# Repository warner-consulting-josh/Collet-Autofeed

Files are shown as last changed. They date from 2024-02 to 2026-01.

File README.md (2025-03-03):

# Collet-Autofeed

Automation of Collets on the Tormach Slant Pro lathe using a custom tooling block, individually addressable coolant lines controlled by an [UnexpectedMaker ProS3](https://esp32s3.com/pros3.html) and ui_hooks.py, and custom G-code for auto stock advance.

## Description

This project uses the uihooks.py [Plugin controller](http://xoomspeed.com/CNC/pathpilot/plugins/uihooks.htm) created by David Loomes at XoomSpeed, to run custom python code for interacting with a ProS3 microcontroller which in turn controls solenoids to direct the coolant stream to the currently active tool. We've also implemented custom G-code to auto advance the stock after each part with a GUI for inputting the stock length at the beginning of the run. (The stock input GUI only works on earlier versions of PathPilot, but it is not reequired for the rest of the system to function)
The hardware includes a custom tooling block, a manifold for the solenoids, a main board with the microcontroller and relays, a connector board to break out the relay lines, and enclosures for both boards.

## Getting Started

### Dependencies

* PathPilot V2
* PathPilot Plugins by [Xoomspeed](http://xoomspeed.com/CNC/pathpilot/plugins.htm)

### Installing

* Follow the instructions from [Xoomspeed](http://xoomspeed.com/CNC/pathpilot/plugins.htm) for intstalling the PathPilot Plugin framework
   * The specific plugin for running the coolant controller is [here:](https://github.com/warner-consulting-josh/Collet-Autofeed/blob/main/PathPilot%20Python/ProS3Cool_plugin.py)
* The circuitpython code that runs on the microcontroller is [here:](https://github.com/warner-consulting-josh/Collet-Autofeed/blob/main/ProS3%20CircuitPython/code.py)
   * Note that the file must be named code.py for the microcontroller using circuitpython to recognize and run it 

### Circuit Boards

* Gerber files for ordering the circuit boards are [here:](https://github.com/warner-consulting-josh/Collet-Autofeed/tree/main/KiCAD/Addressable_Coolant_Controller/gerber_to_order)
* boards were designed in KiCAD using a multi-board workflow with [KiKit](https://yaqwsx.github.io/KiKit/v1.4/multiboard/)

## Authors

Contributors names and contact info

Josh Warner  
joshua@warner-consulting.com

## Version History

* 1.0.0
    * Initial Release

## License

This project is licensed under the [GPL-3.0-only](https://opensource.org/license/gpl-3-0) License

## Acknowledgments

Inspiration, code snippets, etc.
* [XoomSpeed](http://xoomspeed.com/index.htm)
* [KiKit](https://yaqwsx.github.io/KiKit/v1.4/)
* [awesome-readme](https://github.com/matiassingers/awesome-readme)
* [PurpleBooth](https://gist.github.com/PurpleBooth/109311bb0361f32d87a2)
* [dbader](https://github.com/dbader/readme-template)
* [zenorocha](https://gist.github.com/zenorocha/4526327)
* [fvcproductions](https://gist.github.com/fvcproductions/1bfc2d4aecb01a834b46)

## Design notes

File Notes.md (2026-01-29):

# Notes

**PathPilot**

Need to find ways of ensuring that modemmanager does not kick the ProS3 into REPL
- Try this: [Addition to rules file](https://www.metrel.si/support/confluence/mpd/en/software-troubleshooting/how-to-communicate-with-instruments-under-linux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,to%20use%20specific%20USB%20device)
- and this: [rules file](https://www.downtowndougbrown.com/2016/10/fix-for-usb-serial-port-being-opened-by-modemmanager-at-startup/)
- [remove modemmanager](https://superuser.com/questions/568502/usb-device-blocked-at-startup-by-modem-manager) if the above doesn't work
- See if there is a way to ignore the commands in the circuitpython code

Need to figure out how I got custom M-codes fucntioning in the past to prompt the user for bar length and part type
- Look into remap.py and figure out what you did with it before
- Have a file named custom_m_code.py
  - Figure out how to plug this into pathpilot
  - Do I copy paste into the existing tormach remap file?
  - Do I add something to toplevel.py?
- Try following instructions [here](https://forum.linuxcnc.org/20-g-code/33642-custom-m-code-python)
- Confirmed to have working version of remapped M-codes on old pathpilot virtual machine
  - Looking into differences between two versions
  - Found some minor differences, but correcting the file in the new pathpilot did not address the issue
    - This is likely a pathpilot version difference that is causing the problem, something with Tkinter.py
  - The issue is occuring when calling M22, it seems like M20 is parsed immediately when the Gcode is loaded
    - Is my list being lost?
    - Add lots of comments/error messages to figure out where things are going wrong
- **parameter file name is missing**
  - This is caused when you comment out one of the remap definitions
  - Will cause linuxcnc to hang and become non-responsive
  - If you have anything called out as remapped in the ini file make sure it is defined in the remap.py file
- is_callable(oword.m22remap) = FALSE
  - Need to figure out how to fix this to get messages to print, probably also part of the issue in getting the dialog boxes working
  - This error is related to python files calling other python files
    - You can only go 2 layers deep before it stops functioning
    - Effecctively that means all python needs to be in remap.py because it can't call other python files properly
    - linuxcnc forum user bevins discovered this bug and it doesn't appear to have been fixed as of yet
    - likely this makes it impossible to use the custom M-code architecture for user prompting under newer versions of pathpilot
    - will check with latest release 2.10.1

**Microcontroller**
- Here's some info on the [ADC](https://docs.espressif.com/projects/esp-idf/en/v4.4/esp32s3/api-reference/peripherals/adc.html)
- Looks like the ADC is set to -11dB (full range of measurement) by [CircuitPython](https://github.com/adafruit/circuitpython/issues/8754)
  - This means that my conversion to voltage is Vin = (reading / 65535) * reference_voltage
  - Where reference_voltage is 3.3v

**Electronics**
- Relay outputs
  - Look at this [suggestion](https://electronics.stackexchange.com/questions/449872/relay-control-by-using-microcontroller) using optocouplers
    - Andrew suggested that I don't need the external BJT since the chosen optocoupler has an internal one sufficient to drive the relay directly
    - Andrew suggested to use active low signal with push pull mode if using the on board voltage regulator
      - if using a separate voltage regulator, use open drain mode with internal pull up resistor enabled
      - [here](https://docs.circuitpython.org/en/latest/shared-bindings/digitalio/index.html) is how to set the pin mode
    - added an indicator LED across the relay coil directly so that we know when the relay is supposed to be on visually
  - Relay Options:
    - [G5V-1-T90 DC24](https://www.digikey.com/en/products/detail/omron-electronics-inc-emc-div/G5V-1-T90-DC24/6650357)
  - LED:
    - [150120BS75000](https://www.digikey.com/en/products/detail/w%C3%BCrth-elektronik/150120BS75000/4489933)
  - Optocoupler:
    - [PC365NJ0000F](https://www.digikey.com/en/products/detail/sharp-socle-technology/PC365NJ0000F/720501)
- Connection to solenoids
  - VDW22JA by SMC bought [here](https://us.misumi-ec.com/vona2/detail/221006494761/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)
  - Power consumption: 3W
  - Voltage: 24 Vdc
  - Current: 125 mA
- Socket for ProS3?
  - ESP32-S3 GPIO pins each can source 40mA max, prefer to keep at 20mA (does this need power other than USB?)
- Power input
  - 3.3v or 5v for ProS3?
    - can accept both, will be getting some power from the usb (500mA?)
    - might want isolated voltage regulator for powering optcouplers? (total current draw = ?)
  - 24v for solenoids and relays

High Level Architecture
- Main board with micro controller socket, relays, LEDs, screen connection
  - Housed in waterproof enclosure with clear top, either on wall or next to operator screen
- Daughter board with relay connector sockets, big cable connector socket
  - Housed in waterproof enclosure mounted to lathe bed
  - Single cable running back to main board
- Connector board with socket for power, big cable, and USB (maybe passthrough)
  - Housed in same enclosure as Main board
  - Connects to main board with ribbon cable
  - Might instead be just snap lock connectors for power and relay control 
- Board for screen?
- Need to make diagram (draw.io?)

**KiCAD**
Need to design PCBA - Use [KiCAD](https://www.kicad.org/)
- Submodule errors:
  - If encountering this error message: `The following untracked working tree files would be overwritten by merge:`
    - Go to the offending file in the submodule directory **inside** the main project direcotry and delete it
    - **Never** add files to the submodule directory inside the main project directory, **always** add them to the submodule folder outside the project directory
    - Specifically for this project:
      - **Never** add here: `C:\Users\Josh\Dropbox\JOSHUA\Warner Consulting\Collet Autofeed\Github\Collet-Autofeed\KiCAD\Warner-Consulting-Libraries`
      - **Always** add here: `C:\Users\Josh\Dropbox\JOSHUA\Warner Consulting\Collet Autofeed\Warner-Consulting-Libraries`
    - After adding files to the correct folder, to get them to mirror to the project folder:
      - Open gitbash in the project directory
      - `git submodule update --remote --merge`
  - If encountering this error message: `This submodule has modified and untracked changes`
      - Head into the submodule's directory and make sure there isn't anything being built (an output of some kind) w/o you knowing.
      - `cd submoduledir/`
      - `git status`
  - If you see any untracked files in here, just do this to remove them:
      - `git reset --hard HEAD`
      - `git clean -fxd`
- When you need to edit a footprint, **DO NOT** use the "Edit Library Footprint..." option in the properties tab
  - Doing so will cause a conflict with the git submodule
  - Instead, open the global footprint library, make changes, then update the submodule
    - this is a bit cumbersome, but will avoid errors
    - Global and project specific libraries of the same component must have different nick-names in order to be able to edit the global library
  - If `HEAD detached` (updates in global library not reflected in project specific library)
    - `git switch main`
    - `git pull` 
- Silkscreen graphics
  - Can export .dxf from solidworks in whatver orientation I like
  - Used Photopea to create .png with stroke applied to lines and front face filled in
    - Black and white image bigger than I would like the final graphic to be on the board
  - Import .png into KiCAD image converter
    - Check the front silkscreen option and the footprint option
    - Scale to the size I want the graphic to be
    - Create new folder in the library for the new footprint and a .pretty folder inside that
    - Save the footprint in the .pretty folder
  - Push update to submodule up to github
  - Run submodule update command using gitbash
  - Add the footprint to the project specific library list
  - Add footprint onto PCB
- Multi-Board
  - not natively supported, but looks like KiKit can do it
    - install [kikit](https://yaqwsx.github.io/KiKit/v1.4/installation/intro/) using the manager inside KiCAD
    - then install [backend](https://yaqwsx.github.io/KiKit/v1.4/installation/windows/#installation-on-windows) using KiCAD Command line: `pip install kikit`
    - finally, install the [libraries](https://yaqwsx.github.io/KiKit/v1.4/installation/gui_and_libs/)
  - Set up the KiCAD project with a top-level schematic that has sub-schematics in it which each represent a board
    - The top level schematic will have the board to board connections 
  - no global labels for power or anything else, just local labels
  - [guide](https://yaqwsx.github.io/KiKit/v1.4/multiboard/#multi-board-workflow-with-kikit)
  - Board annotation for separation uses "virtual footprint"
    - kikit:board is a footprint in the library
    - Place a copy of kikit:board for each board outline
    - Rename the ref** text to the name of the board
      - **No spaces in the name** it will screw with the command for separating the boards
    - Need to make sure arrow point on kikit:board is exactly touching one of the lines in the edge cut for the board
      - use the coordinate properties from the board outline and paste them into the arrow properties
    - cd to folder containing *source_multi-PCB*.kicad_pcb
      - make sure to save board design before running command
    - run command for each board
    - `kikit separate --source "annotation; ref: *board_name*" *source_multi-PCB*.kicad_pcb *destination_single-PCB*.kicad_pcb`

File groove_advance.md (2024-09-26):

# groove_advance workflow and assumptions

**Workflow**
1. Move to starting spot (Z0)
2. Change to T81
3. Move clear in X
4. Move to end of part (Z-[#<_Groove_Start>])
5. Cut groove
6. Move to safe tool change location
7. Switch to T89 (pickle fork)
8. Move to groove and capture stock
9. Unclamp collet
10. Advance stock
11. clamp collet
12. Move clear in X
13. Move to safe tool change location
14. Change to T81
15. Cut off hat

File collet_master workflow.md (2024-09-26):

# collet_master workflow and assumptions

**Workflow**
1. Define global variables
   - #<_Length> = XX (Length of bar stock in inches)
   - #<_Remnant> = 1 (Length of remnant for collet to grip)
   - #<_Body_Length> = 1.175 (Length of Body piece)
   - #<_Nut_Length> = 0.6 (Length of Nut piece)
   - #<_Advancing_Length> = 0.283 (Length of material needed for cleanup and bar pulling)
   - #<_one_or_two> = 1 (1 = body 2 = nut)
2. User input dialog box (currently not working, need to downgrade pathpilot)
3. Part count calculation based on previously defined variables
4. Loop correct number and type of part
   - Check whether nut or body and go to corresponding subroutine
   - Run groove and advance subroutine
5. Finish program and print debug statements with number and type of parts

**Assumptions**
- Separate subroutine files for nut, body, and groove advance
- Subroutine folder path has been added to .ini file

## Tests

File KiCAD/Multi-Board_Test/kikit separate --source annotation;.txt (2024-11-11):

kikit separate --source "annotation; ref: B1" multiboard.kicad_pcb board_a.kicad_pcb

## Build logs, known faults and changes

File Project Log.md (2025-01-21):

# Project Log
Notes on what I did each day so that I can keep track of my changes and remember where/what I was working on

**01/22/2024**
- Installed Mu and plugged in TinyS3 Pro
  - Defualt code running
- Downloaded latest ui_hooks.py and installed into OLD PathPilot VM
- Commented out lines in ~/tmc/python/pathpilotmanager.py so that I don't have to pick configuration of machine every time
```
# state of the VM leftover from a previous student.
#            if os.path.exists(PATHPILOTJSON_FILE):
#                os.unlink(PATHPILOTJSON_FILE)
#                print "Removing config file to force selection of machine type in sim mode."
```
- Installed ToolPrint_plugin.py on OLD Pathpilot VM and verified it is working

**01/23/2024**
- Added "UnexpectedMaker ProS3 [0100]" to USB Device filter with USB 3.0 Controller enabled
  - CIRCUITPY drive shows up in Linux
- Added 99-ProS3.rules to /etc/udev/rules.d
```
ACTION=="add",SUBSYSTEMS=="usb",KERNEL=="ttyACM*",ATTRS{manufacturer}=="UnexpectedMaker",ATTRS{product}=="ProS3",SYMLINK+="ProS3",GROUP="dialout",MODE="0666"
```
- Modified TinyS3io.py to ProS3Cool.py and tryed to get a serial connection working
  - Plugin runs but does not successfully invoke TryToConnect()
  - Need to look into syntax and figure out why it isn't calling the function
**01/23/2024 update**
- Successfully invoked TryToConnect()
  - Previously: `self.ComPor.TryToConnect()`
  - Corrected: `self.TryToConnect()`
- Added some debug and error prevention to ProS3_plugin.py

**01/24/2024**
- Worked on getting the ProS3 to respond to data sent by the ProS3Cool plugin
- Got the microcontroller to respond to serial data sent using Mu
- Currently getting a unicode? error that causes the ProS3 to exit it's code loop and enter the REPL

**01/25/2024**
- Successfully established 2 way serial communication between the ProS3_plugin.py code and the ProS3 microcontroller
  - Needed to disable modemmanager in linux because it was causing the ProS3 to enter REPL
  - run `sudo service modemmanager stop` in the linux terminal
  - Need to investigate handling the issue in the microcontroller's code
  - Need to uninstall the modemmanager
    - `sudo apt-get purge modemmanager`

**01/26/2024**
- Worked on electronics side instead of code
  - want to get a relay output circuit put together so that I can toggle a solenoid using the code
- Got a first draft of the relay driver circuit drawn in KiCAD and approved by Andrew and Jordan
  - using optocoupler to drive a relay with an indicator LED and freewheel/flyback diode in parallel across the relay coil
  - want to use active low pins to drive the circuit according to Andrew

**01/29/2024**
- Talked with Andrew about pin modes for output
  - Want to go with push pull if using on board voltage regulator (current plan)
  - use open drain with internal pull up if using separate voltage regulator
- Verified oring sizing for manifold block using Erik online gland calculator
- Ordered oring and screws to connect top and bottom half of manifold block

**01/30/2024**
- Looked into adding a watchdog timer to reboot the ProS3 in the event of a communication failure or code error
  - Will need the watchdog timer running on the ProS3 and periodic data being sent by the plugin inside of pathpilot
  - Want to set up the pathpilot plugin to send data every ~2 seconds (pick some time interval that feels comfortable) and call feed() on the ProS3 every time data is received
- Also looked at non-blocking LED blink
  - Will want to make the responses to serial communication non blocking on the ProS3 and make the serial write commands in pathpilot nonblocking
 
**02/01/2024**
- Tried adding a watchdog timer triggered by first successful serial communication on a 2 second timer
  - 2 seconds is way too fast for development purposes, and watchdog should be triggered by a specific serial command/start phrase
  - Got stuck in a boot loop here's how to fix:
    - To get into safe mode, follow these steps:
      1. Press the [RESET] button to reset the ESP32-S3 chip
      2. After the RGB LED has gone purple and then off, press and hold the [BOOT] button for a few seconds
      Your board should now be in safe mode.

**02/05/2024**
- Adjusted watchdog timer to 45s and implemented a keyword to start watchdog ('ProS3')
  - Not sure that keyword is working as intended
  - watchdog timer stays active through resets, may need to actively disable it in code until the keyword is received
  - need to work through the logic of what should happen in the event of failure:
    - Pause the g-code running on the tormach?
    - keep the current coolant solenoid energized? or turn them all off?
    - restart g-code if connection to microcontroller reestablished?
    - wait for user input?
    - only pause if connection not reestablished with X seconds?
    - Talk with EW and make a plan
- Added `print(microcontroller.cpu.reset_reason)` to display the reason for the last time the code was stopped
  - would like to have this displayed on a screen, along with current tool, up time since last reset?

**02/07/2024**
- Removed watchdog timer and added code to toggle gpio pin based on serial input
  - Successfully implemented active low gpio triggering
- Breadboarded relay circuit but had trouble getting relay to trigger

**02/08/2024**
- Found issue with breadboard circuit
  - Flyback diode was reversed which prevented the relay from triggering
- Having some issues with the timing of the LED blink, so will need to look at difference between old and new code

**02/12/2024**
- Added KiCAD to github repository for version control and sync across computers
- Added 24v monitor circuit to circuit schematic
  - Plan to send an error/pause command up to the plugin if 24v power is lost
- Added 4 pin connector for power in of same style as ribbon cable connector that goes to the solenoid connection daughter board
  - Plan to have input daughter board with power in and USB in
- Looked at screens
  - Currently have small monochrome OLED [screen](https://www.adafruit.com/product/938)
  - Maybe want bigger [screen?](https://www.adafruit.com/product/5872)
    - Look into power requirements, and how difficult it is to drive each screen
   
**02/15/2024**
- Got KiCAD integrated fully into github using a submodule for the custom libraries
  - Created a separate repository for the [custom libraries](https://github.com/warner-consulting-josh/Warner-Consulting-Libraries.git)
  - Used git bash to add submodule to Collet-Autofeed repository which acts like a symbolic link pointing back to the libraries repository
    - `git submodule add https://github.com/warner-consulting-josh/Warner-Consulting-Libraries.git KiCAD/Warner-Consulting-Libraries`
  - Need to use `git submodule update --remote --merge` any time there are changes to the libraries repository (adding componnets, updating step files, etc.)
- Evaluated several header connectors and replaced the Wurth one with a TE AMP-Latch [connector](https://www.digikey.com/en/products/detail/te-connectivity-amp-connectors/1761685-6/2187846)

**03/01/2024**
- Successfully integrated basic display code with serial read code
  - Displayed current tool number on OLED using Mu, Pathpilot virtual machine, and actual lathe
- Need to decide what information to display
  - Current tool
  - Reason for last restart
  - Up time?
    - Will this cause issues with code blocking?
- Need to get larger screen
  - E-ink?
  - Big OLED?
  - Colored screen?

**09/03/2024**
- Powered up breadboard circuit and confirmed code works and displays current tool
  - Confirmed code working with Mu, and Pathpilot virtual machine
- Tried to get wrapper .nc program running for multiple part operation
  - Ran into issue with remapped M-Codes
  - Need to investigate further because I had this working before
  - Look into remap.py and the INI file for the lathe
  - Have python with remaps defined, need to figure out how exactly it was integrated into pathpilot

**09/05/2024**
- Worked on getting custom M-code working again
- Did not find anything terribly useful
  - Most links seem to just point back at the one post that shows how to make the M codes but doesn't have a solution to the index out error
- This was working at some point in the past
  - Maybe boot up old laptop and see if you can make it function there

**09/06/2024**
- Continued working on getting custom M-codes working
- Booted old laptop and have functioning code in onld version of pathpilot
- Same code does not work in new version of pathpilot
- Code is having trouble calling dialog = Tk()
  - When I run this on it's own in python, it works
  - It looks like pathpilot is using python 2.7, not 3.x
- Added an error message to M20 and it forced an error immediately on loading Gcode, not when I run it

**09/09/2024**
- Continued with custom M-codes
- Caused and then fixed error: parameter file name missing
  - Don't comment out any of the remaps in the remap file
- Currently dealing with is_calable(oword.m22remap) = FALSE
- Stripped the remapped M-code functions down to only displaying messages that they were called, but no message shows up, likely due to the above
- Probably also part of why the dialog boxes are not functioning
- Further research on the linuxcnc forum required

**09/10/2024**
- Figured out how to snapshot virtualbox
- Updated pathpilot inside virtualbox to latest version 2.10.1
- This erased my changes in the .ini and custom M-code stuff, so I will need to re-introduce them to test if this still has the issue with nested python calls

**09/24/2024**
- As far as I can tell, I will not be able to get user prompting running under later versions of PathPilot
  - Will need to revert machine to v2.2.4 (figure out latest version that will work)
- Got subroutine code working
  - Needed endif statement for every if statement (elseif does not function as endif)
  - Needed endsub for one of the routines
- Got external named subroutine working
  - Needed to add subroutine path to .ini file
  - Need to make sure subroutine file is executable
  - o<filename> sub/endsub/call (where filename is the name of the subroutine file without the .nc extension)
- Moved groove and advance code into external subroutine
- Need to move body and nut code into external subroutines
- Need to add grooving stock requirement to part per bar calculations
- Need to add part number override for running n parts explicitly until we get user prompting working

**09/30/2024**
- Got the code transfered over to the lathe and have collets running multiples at a time
  - Need to copy the working code from the lathe into the github so that it is accurately represented
- Looked at the state of electronics
  - Enclosure and connectors that I had previously ordered
  - Drew a crude architecture diagram, need to transfer that into a more refined format draw.io?
  - Plan to have small enclosure on lathe bed with connections to relays on a board that connects to a larger (10 pin) cable
  - 10 pin cable connects to main board in housing that is stationary
    - Either mounted on wall or on operator console
  - Main board enclosure has screeen, relays, microcontroller, power connection, relay control connection, USB connection
    - USB will be pass through (have gland pieces)
    - Power and relay control will be snap lock type connectors
    - No ribbon cable, no daughterboard in this enclosure
    - Will need to mount screen in here somehow
      - Don't want to block relay LEDs
      - Can use little connector cable directly from micro, or could use pins and headers
     
**10/03/2024**
- Drew a basic architecture diagram in draw.io
- Started designing relay connector board and enclosure
  - Will use 10 pin connector and snap lock to connect to PCB with 8x 2 pin connectors
  - Plan to machine enclosure from solid piece of delrin and use O-ring to seal lid
    - 3D print before machining to ensure everything fits
   
**10/08/2024**
- Finished design of relay connector board enclosure
- Need to double check O-ring gland design
- Will be machined from large block of delrin with clear acrylic lid
- Need to adjust mounting board to fit new design
- Need to work on PCB layout for connector board
- Need to work on design of enclosure for main board with screen

**10/11/2024**
- Tried using big screen, looked like more effort than I was up for this morning
- Do we actually need big screen?
  - Screen is more of a diagnostic tool/passive information display
  - Focus should be on getting system functional and then adding features later if we want them
  - Design enclosure for small screen and deal with big screen later
- System is fucntioning, so we should get some PCBs and enclosure
- Need to machine solenoid manifold
- Need to machine connector board enclosure

**10/14/2024**
- Added `ignore = dirty` to gitmodule file to deal with untracked changes issue in github
- Started placing components into mcmaster washdown enclosure, but had to deal with github issues for most of the morning

**10/15/2024**
- Replaced ribbon cable connector with 10-pin molex connector on main board schematic
- Started placing connectors and board supports in mcmaster enclosure model
- Fixed issues with libraries and added library for molex connector
- Need to double check that libraries are properly syncing because one of my footprints was missing
- Need to add board clearance to board support piece

**10/17/2024**
- Actually fixed issue with submodule
  - Had created file inside mirrored folder instead of in base repository folder, see notes for details
- Added 2 pin power connector to schematic
- Updated board outline to new size and started positioning components

**10/22/2024**
- Placed components on PCB and completed initial routing
- Still need to add power and ground planes
- Need to figure out why labels are not showing on silk screen
- Need to add silk screen demarkations for solenoid to LED correlations
- Probably should add a logo and some other identifying information to the silk screen as well

**10/23/2024**
- Replaced PC365NJ0000F surface mount opto-isolator with PC12311NSZ1B through hole
- Added power and ground fills on top and bottom layers respectively
- Need to figure out why changes to 10-pin and 2-pin connectors didn't save/propagate to other computer
- Need to figure out silkscreen labels not showing for components

**10/24/2024**
- Added rectangle representing screen into the silkscreen layer
- Sketched screen board outline in solidworks in the part file of the box
- Need to figure out screw size and standoffs
- Need to add screw holes into main board
  - Consider 3d printed screen support as alternative
  - Might be somewhat spidery, but maybe it would work with standoffs
 
**10/25/2024**
- Fixed silkscreen labels for components
  - Had to mess with library footprints and update the footprints on the pcb
- Replaced remaining surface mount opto-isolator with through hole
- Adjusted screen mount to used OTS standoffs

**10/28?2024**
- Figured out how to add custom silkscreen graphics
- Added logo to silkscreen
- Fixed issue with step file of LEDs disappearing

**10/29/2024**
- Added zones and zone labels to silkscreen
- Added "Addressable Coolant Controller v1.0.0" to silkscreen
- Added company name, my name and date to silkscreen
- Need to make connector board and model screen into assembly
- Need to review finalized board before sending for manufacturing

**10/30/2024**
- Changed name of KiCAD project to Addressable Coolant Controller
- Moved KiCAD files into subdirectory named per previous
- Looked into multi-board project workflow in KiCAD
  - is not natively supported, but the plugin KiKit can do it
  - installed KiKit and will try doing a multiboard project
  - want to have main board and connector board with shared pinout for connector between them
 
**10/31/2024**
- Created Multi-Board Test project to figure out the multiple board in one project workflow
- Made top level schematic with inter-board connector and heirarchical labels to pass pins down into each board sheet
- Made one PCBnew file with both boards in it
- Need to figure out annotation for board separation
  - Something about "virtual footprints"

**11/04/2024**
- Got multi-board workflow functioning on a test project
- Added instructions to notes.md on how to implement this workflow
- Dad asked to add pressure sensor to system to detect coolant flow

**11/05/2024**
- Ordered pressure sensor from amazon
  - 0.5v-4.5v output, 5v input, 100psi max
  - 3 wires: VCC, GND, Output
  - will need a voltage divider to step down to 3.3v for ProS3
  - will need to implemnet code to read signal input
 
**11/07/2024**
- designed voltage divider low pass filter circuit
  - chose 10Hz as cutoff freq
  - resistor and capacitor values in Parsify file
- looked at 12 pin connectors for accomodating the pressure sensor on the connector board
  - omron internal connectors come in 12 pin variant -> easy change
  - found 12 pin circular connector from Amphenol
    - need to evaluate the size impact on connector board enlcosure
    - components to make a cable are ~$175
    - premade cables are out of stock but only ~$30 -> 4 week lead time from mouser

**11/08/2024**
- found 4 pin connector for pressure sensor
  - same family as 2 pin connectors for solenoid connections
- added 9th hole in connector enclosure for pressure sensor connector
- added 12 pin connector to connector board assembly
  - need to adjust sketch to match dimensions of new connector
- added 12 pin board connector and adjusted sketch to match
  - needed to modify 10 pin connector because SnapEDA kept downloading the wrong one for the 12 pin
  - will need to add to the library repo
  - will need to double check footprint
- ordered 12 pin connector, 12 pin board connector, 12 pin board connector mate, short 12 pin cable, 4 pin connector, 4 pin cable
- ordered long 12 pin cable from mouser on backorder, 4 week lead time
- main lathe assemlby is broken and will not open on my computer, will need to remake
- discussed overall assembly of tooling block, solenoid block, and connector board assembly on big plate
  - want to be a complete unit
  - need to make it easier to put on and off the lathe
  - want to reduce swarf build up in lower corner

**11/13/2024**
- got footprint and symbol customization workflow ironed out
  - have global libraries of symbol and footprint
    - tied directly to the Warner-Consulting-Libraries repo
    - changes here update the repository
  - after updating the repository files, update the submodule and the changes will be reflected
- put 12 pin connector into top level schematic
- added voltage divider circuit into sub sheet and add heirachical label sheet pins to pass the nets in and out
- assigned IO13 to reading the output from the pressure sensor off the voltage divider
- fed 5v out from the MCU to power the pressure sensor
  - pressure sensor is stated to draw ≤3mA, should be safe to power from MCU
- will need to double check component values for voltage divider and order them
- will need to export board outline from solidworks with placements for the connectors
  - will need to figure out how to line up connector footprints with specified locations on board outline

**11/14/2024**
- measured pressure response of 100psi pressure sensor
  - very linear, made an excel sheet to visualize data
  - output is ratiometric to input voltage
    - this means I can use 3.3v to power it and won't need a voltage divider for the GPIO
- want to use a 30psi sensor instead
  - ordered one on amazon in same form factor
- fixed the broken netclasses in the schematic
- removed the voltage divider circuit and heirarchical sheet
- added some info to the title block of the sheet
  - need a version of the logo with no color in the background
  - could also make it a blue logo

**11/15/2024**
- ordered solder cup version of 12 pin connector
- fixed 12 pin connector sketches in connector board skeleton
- sized oring gland in connector board skeleton
  - make sure that the connector board with all components is able to slide in from the top
  - make sure oring gland is sized for off the shelf oring
- need to make keying feature on 12 pin connector cutout

**11/18/2024**
- made subassembly for entire tooling plate with block, solenoid manifold, and connector board
- adjusted 12 pin connector cutout to have proper shape for keying
- sized o-ring gland for both solenoid manifold and connector board housing
- made simplified slant pro assembly
  - need to adjust range of motion in assembly and finish making the moveable comonents

**11/22/2024**
- added connector board outline and circular connector locations to the pcb file
- updated schematic with circular connectors and added the propper netclasses
- added libraries for the circular connectors
- updated pcb with changes from schematic and now I need to fix the routing and placement of components
  - component designators got moved around and now components are all scrambled on the board

**11/25/2024**
- updated all component designators and locations on board
- fixed netclass issues and rerouted all ratsnest items
- routed connector board
  - need to add copper fills for ground plane
- need to fix missing 3d models on some LEDs
  - probably need to update the LED footprints at the library level (global library tied to the repository)

**11/26/2024**
- added LEDs to connector board
- moved LEDs and accompanying resistor and connector into heirarchical sheet for easy circuit and layout duplication
- fixed LED footprints and missing models
- added board outline annotations for splitting using kikit
- exported step file and added to solidworks subassemblies
- need to get a top level assembly functioning
- need to redo pressure characterization with 30psi sensor
- need to start coding the pressure sensor into the microcontroller
- finalized board designs and sent to JLCPCB for manufacture
  - shopped around and they were by far cheapest
- made Warner Consulting logo a soldermask/copper logo and use ENIG for gold apperance on final board
  - [copper graphic element](https://forum.kicad.info/t/shouldnt-copper-only-symbol-footprints-have-have-solder-mask-removed/45087/2)
- added "Designed in KiCAD" logo as a copper element for subtle effect
- do we want to make this design open source?

**12/02/2024**
- Created interactive HTML BOM using KiCAD external plugin
- ordered remainder of board components
- want to 3D print connector board enclosure and assemble with fasteners and oring
- want to 3D print main board mount and screen mount
  - need to order fasteners, standoffs, and enclosure from McMaster

**12/11/2024**
- Over the last few work days I have populated 1 each of the main board and connector board
- Fit checked the connector board in a 3D printed enclosure with laser cut lid
  - laser cutter needs some sort of calibration/maintainence, it was cutting oversized and out of square
- ordered wires and ferrules to make wiring harness for connector board and main board
- ordered slightly-nicer-than-amazon-quality ferrule crimpers from Ferrules Direct
- started 3D print of manifold block to fit check
- fit checked manifold block with all solenoids and pressure sensor
  - still need to get input fitting and o-ring
  - still need to check the press-in push-to-connect fittings, but the print geometry was not good in that area
  - reprint a single widget with those holes facing upwards

**12/13/2024**
- Adjusted design of screen mount and printed so that screen avoids gate in clear enclosure lid and also logo
- made wiring harness for 24v from bench power supply for testing code changes without being hooked up to lathe
  - crimp on bootlace ferrules work beautifully in omron connector, insulation is perfectly sized
- started widget print for fit checking the press-in push-to-connect fittings

**12/16/2024**
- Mapped pins in code to board pins and tested function with main board
- Added power monotor code
  - will need to figure out how to pass this info back to linuxcnc
  - will need to figure out how to pass current tool info back to linuxcnc (heartbeat? watchdog? look more deeply into this)
- need to figure out how to map tool numbers to solenoid numbers (dynamically?)
  - look at having a preamble in the gcode or something in the python plugin code to communicate this info to the microcontroller
- Added first step towards having pressure sensor

**12/17/2024**
- Received wires from wire barn
- Started organizing all hardware into Sortimo project box
  - Using label maker for each bin with description, PN, applicable tool, material, QR code link, etc.

**01/01/2055-01/06/2025**
- Wired pressure sensor up to the 4 pin connector and added code to microcontroller to read ADC input
  - Need to convert raw ADC value to PSI value
  - Need to measure ADC value with known pressure to create calibration curve
- Organized electrical components into Sortimo box with labels
- Need to make cutouts in enclosure for connectors
- Need to machine Connector Board enclosure
- Need to machine solenoid manifold block

**01/09/2025**
- Used ChatGPT to transition existing PathPilot plugin code into a state machine format
- Created stat transition diagram and used Draw.io to digitize it
- Will need to test the code to prove functionality
- Need to transition microcontroller code to state machine and define what messages to send back to the PathPilot plugin

**01/10/2025**
- Got the state machine architecture working on for the PathPilot plugin
- Used ChatGPT to transition the microcontroller code into a state machine format
  - Will need to creat state transition diagram for microcontroller code
- Having some issues with funky messages received by the PathPilot plugin
  - need to figure out exactly what the microcontroller is sending and clean that up
- Want to have tool number verification
  - want the PathPilot plugin to get confirmation that the microcontroller has the correct tool

**01/20/2025**
- Got the microcontroller sending it's tool number, power status, and pressure data periodically out over serial
- Plugin code now listens to that data and has some error responses
  - If program is running and power has been off for X seconds, stop the program
  - If program is running and tool number received does not match that in the spindle (after X second delay), stop the program
- Need to convert pressure integer data into PSI
  - Then need to do something with that
    - Check if coolant is supposed to be on, then check if pressure has been trending down/goes below a threshhold, then stop the program
- Need to look at disconnection failures and attempting to reconnect

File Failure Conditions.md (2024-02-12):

# Failure Conditions and Response Strategies
**Failure Modes**
1. Power loss to microcontroller
2. Power loss to solenoids
3. Code crash
4. Serial communication lost

**General Thoughts**
- Not haveing coolant isn't like not having air, more like not having water
  - Need to fix the problem, but don't need to stop instantaneously
  - Have ~30-60s to respond?
- Want to check status of microcontroller after each operation?
  - Don't like that this needs to be added to the G-code
    - might be able to detect an operation change similar to how a tool change is detected
    - don't like the variability in length of time of the operations (time without coolant could be as long as longest operation)
  - Would prefer to have the status check built into the plugin
- Want to check the status of microcontroller every X seconds?
  - "Hearbeat" sent from microcontroller and listened to by plugin
  - Watchdog timer on microcontroller to reset in case of code failure
- How many times/how long should plugin try to reconnect before issuing a pause command?
  - use "TryToConnect" function for X seconds or X times
- Should we have a fallback coolant nozzle that is fixed to the headstock?
  - turns on if there are issues with the plugin/microcontroller
  - allows finishing current part?
- Want to display message about why the microcontroller failed/reset/restarted
  - send message to plugin
  - also display on small screen directly on microcontroller
  - have a running timer showing how long the microcontroller has been functioning since last reset

**Response Strategies**
1. Power loss to microcontroller
   - leads to serial communication lost
   - try to reestablish communication within acceptable time frame using plugin code
   - else, pause program 
3. Power loss to solenoids
   - leads to no coolant flowing from nozzles
   - could have fallback nozzle that is "fail safe" ie. is the default path that is diverted away from when a solenoid is powered
   - want to feed info about solenoid power back into microcontroller
   - if power not restored to solenoids within X seconds, send pause message to plugin
5. Code crash
   - leads to serial communication lost
   - use watchdog timer to reset microcontroller
   - try to reestablish communication within acceptable time frame using plugin code
   - else, pause program 
7. Serial communication lost
   - try to reestablish communication within acceptable time frame using plugin code
   - else, pause program

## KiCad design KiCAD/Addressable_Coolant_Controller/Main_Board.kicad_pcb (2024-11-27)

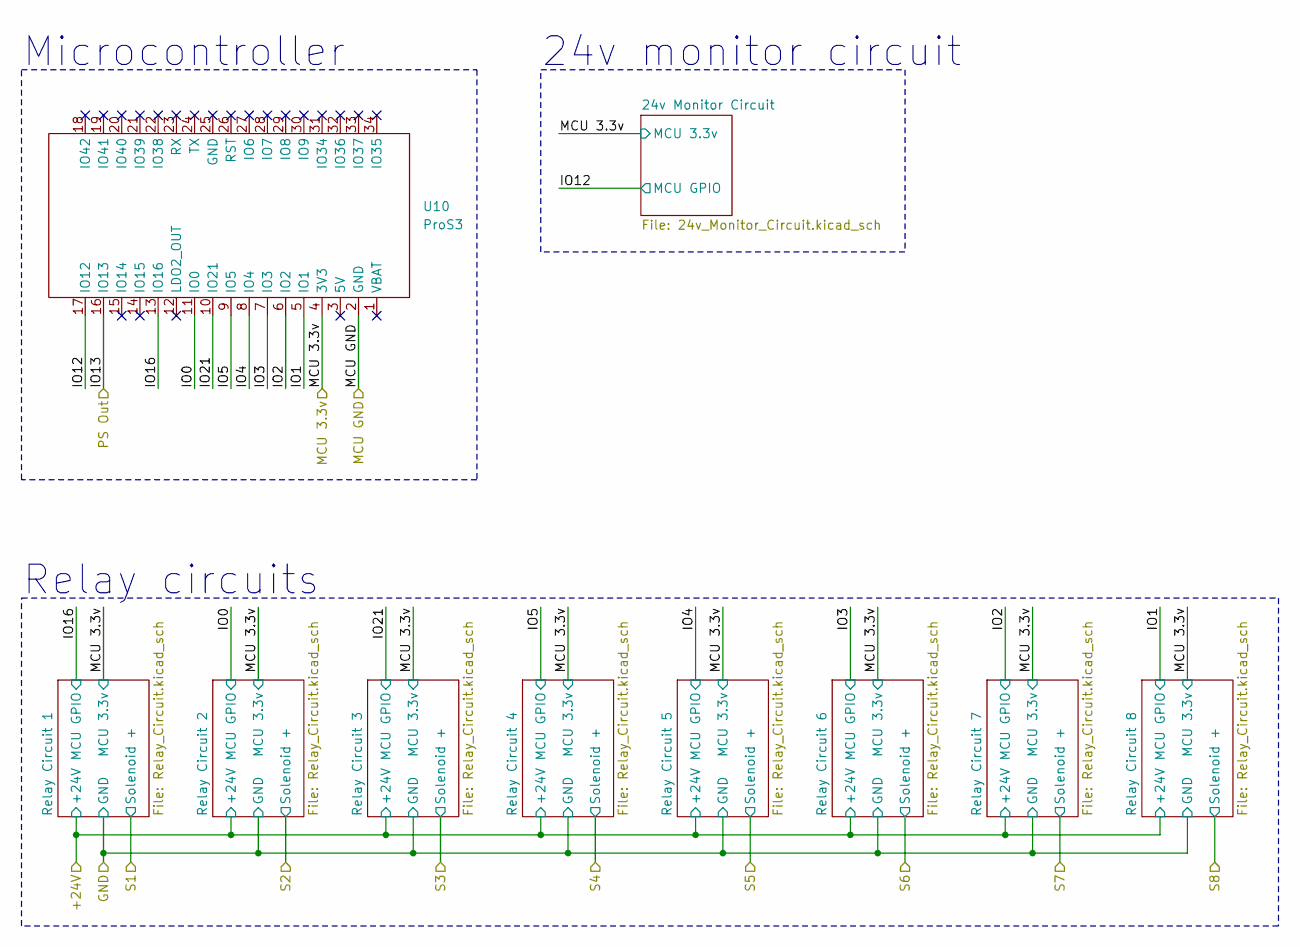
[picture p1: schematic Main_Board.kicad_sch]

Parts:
U10: ProS3; ProS3_TH

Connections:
/Main_Board/IO0: U10.11 (IO0); also elsewhere on the board
/Main_Board/IO1: U10.5 (IO1); also elsewhere on the board
/Main_Board/IO2: U10.6 (IO2); also elsewhere on the board
/Main_Board/IO3: U10.7 (IO3); also elsewhere on the board
/Main_Board/IO4: U10.8 (IO4); also elsewhere on the board
/Main_Board/IO5: U10.9 (IO5); also elsewhere on the board
/Main_Board/IO12: U10.17 (IO12); also elsewhere on the board
/Main_Board/IO13: U10.16 (IO13); also elsewhere on the board
/Main_Board/IO16: U10.13 (IO16); also elsewhere on the board
/Main_Board/IO21: U10.10 (IO21); also elsewhere on the board
/Main_Board/MCU 3.3v: U10.4 (3V3); also elsewhere on the board
/Main_Board/MCU GND: U10.2 (GND); also elsewhere on the board

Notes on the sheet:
Microcontroller
24v monitor circuit
Relay circuits

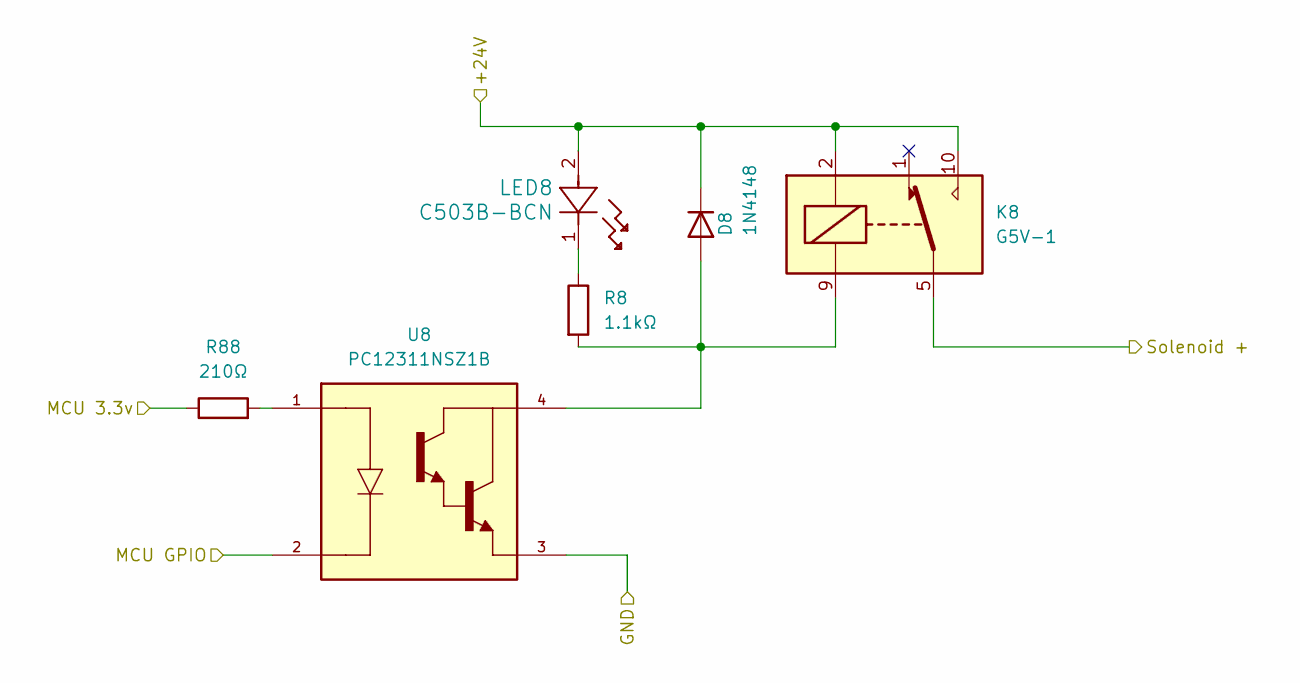
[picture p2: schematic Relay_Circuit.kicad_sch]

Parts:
D8: 1N4148; D_DO-35_SOD27_P7.62mm_Horizontal-JW
K8: G5V-1; Relay_SPDT_Omron_G5V-1
LED8: C503B-BCN; C503B_BCN_CV0Z0461
R8: 1.1kΩ; R_Axial_DIN0204_L3.6mm_D1.6mm_P5.08mm_Horizontal-JW
R88: 210Ω; R_Axial_DIN0204_L3.6mm_D1.6mm_P5.08mm_Horizontal-JW
U8: PC12311NSZ1B; Mouser Part Number 852-PC12311NSZ1B

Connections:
+24V: D8.1 (K), K8.2, K8.10, LED8.2; also elsewhere on the board
/Main_Board/IO1: U8.2; also elsewhere on the board
/Main_Board/MCU 3.3v: R88.1; also elsewhere on the board
/Main_Board/S8: K8.5, K8.6; also elsewhere on the board
GND: U8.3; also elsewhere on the board
unnamed: D8.2 (A), K8.9, R8.2, U8.4
unnamed: LED8.1, R8.1
unnamed: R88.2, U8.1

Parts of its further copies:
D1, D2, D3, D4, D5, D6, D7: 1N4148; D_DO-35_SOD27_P7.62mm_Horizontal-JW
K1, K2, K3, K4, K5, K6, K7: G5V-1; Relay_SPDT_Omron_G5V-1
LED1, LED2, LED3, LED4, LED5, LED6, LED7: C503B-BCN; C503B_BCN_CV0Z0461
R1, R2, R3, R4, R5, R6, R7: 1.1kΩ; R_Axial_DIN0204_L3.6mm_D1.6mm_P5.08mm_Horizontal-JW
R11, R22, R33, R44, R55, R66, R77: 210Ω; R_Axial_DIN0204_L3.6mm_D1.6mm_P5.08mm_Horizontal-JW
U1, U2, U3, U4, U5, U6, U7: PC12311NSZ1B; Mouser Part Number 852-PC12311NSZ1B

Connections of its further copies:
+24V: D1.1 (K), D2.1 (K), D3.1 (K), D4.1 (K), D5.1 (K), D6.1 (K), D7.1 (K), K1.2, K1.10, K2.2, K2.10, K3.2, K3.10, K4.2, K4.10, K5.2, K5.10, K6.2, K6.10, K7.2, K7.10, LED1.2, LED2.2, LED3.2, LED4.2, LED5.2, LED6.2, LED7.2; also elsewhere on the board
/Main_Board/IO0: U2.2; also elsewhere on the board
/Main_Board/IO2: U7.2; also elsewhere on the board
/Main_Board/IO3: U6.2; also elsewhere on the board
/Main_Board/IO4: U5.2; also elsewhere on the board
/Main_Board/IO5: U4.2; also elsewhere on the board
/Main_Board/IO16: U1.2; also elsewhere on the board
/Main_Board/IO21: U3.2; also elsewhere on the board
/Main_Board/MCU 3.3v: R11.1, R22.1, R33.1, R44.1, R55.1, R66.1, R77.1; also elsewhere on the board
/Main_Board/S1: K1.5, K1.6; also elsewhere on the board
/Main_Board/S2: K2.5, K2.6; also elsewhere on the board
/Main_Board/S3: K3.5, K3.6; also elsewhere on the board
/Main_Board/S4: K4.5, K4.6; also elsewhere on the board
/Main_Board/S5: K5.5, K5.6; also elsewhere on the board
/Main_Board/S6: K6.5, K6.6; also elsewhere on the board
/Main_Board/S7: K7.5, K7.6; also elsewhere on the board
GND: U1.3, U2.3, U3.3, U4.3, U5.3, U6.3, U7.3; also elsewhere on the board
unnamed: D1.2 (A), K1.9, R1.2, U1.4
unnamed: D2.2 (A), K2.9, R2.2, U2.4
unnamed: D3.2 (A), K3.9, R3.2, U3.4
unnamed: D4.2 (A), K4.9, R4.2, U4.4
unnamed: D5.2 (A), K5.9, R5.2, U5.4
unnamed: D6.2 (A), K6.9, R6.2, U6.4
unnamed: D7.2 (A), K7.9, R7.2, U7.4
unnamed: LED1.1, R1.1
unnamed: LED2.1, R2.1
unnamed: LED3.1, R3.1
unnamed: LED4.1, R4.1
unnamed: LED5.1, R5.1
unnamed: LED6.1, R6.1
unnamed: LED7.1, R7.1
unnamed: R11.2, U1.1
unnamed: R22.2, U2.1
unnamed: R33.2, U3.1
unnamed: R44.2, U4.1
unnamed: R55.2, U5.1
unnamed: R66.2, U6.1
unnamed: R77.2, U7.1

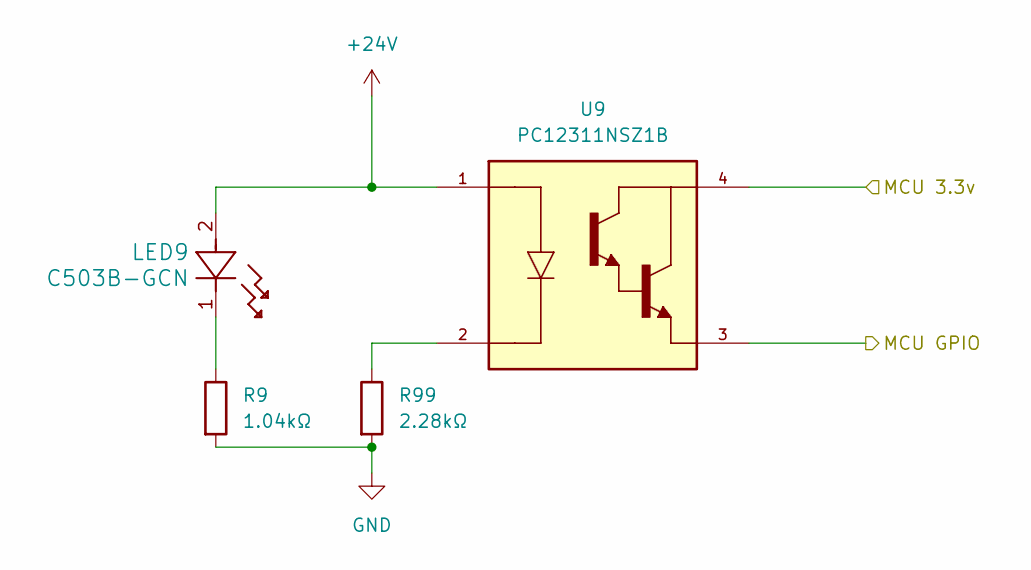
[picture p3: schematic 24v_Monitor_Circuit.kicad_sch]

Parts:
LED9: C503B-GCN; C503B_GCN_CY0C0792
R9: 1.04kΩ; R_Axial_DIN0204_L3.6mm_D1.6mm_P5.08mm_Horizontal-JW
R99: 2.28kΩ; R_Axial_DIN0204_L3.6mm_D1.6mm_P5.08mm_Horizontal-JW
U9: PC12311NSZ1B; Mouser Part Number 852-PC12311NSZ1B

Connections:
+24V: LED9.2, U9.1; also elsewhere on the board
/Main_Board/IO12: U9.3; also elsewhere on the board
/Main_Board/MCU 3.3v: U9.4; also elsewhere on the board
GND: R9.2, R99.2; also elsewhere on the board
unnamed: LED9.1, R9.1
unnamed: R99.1, U9.2

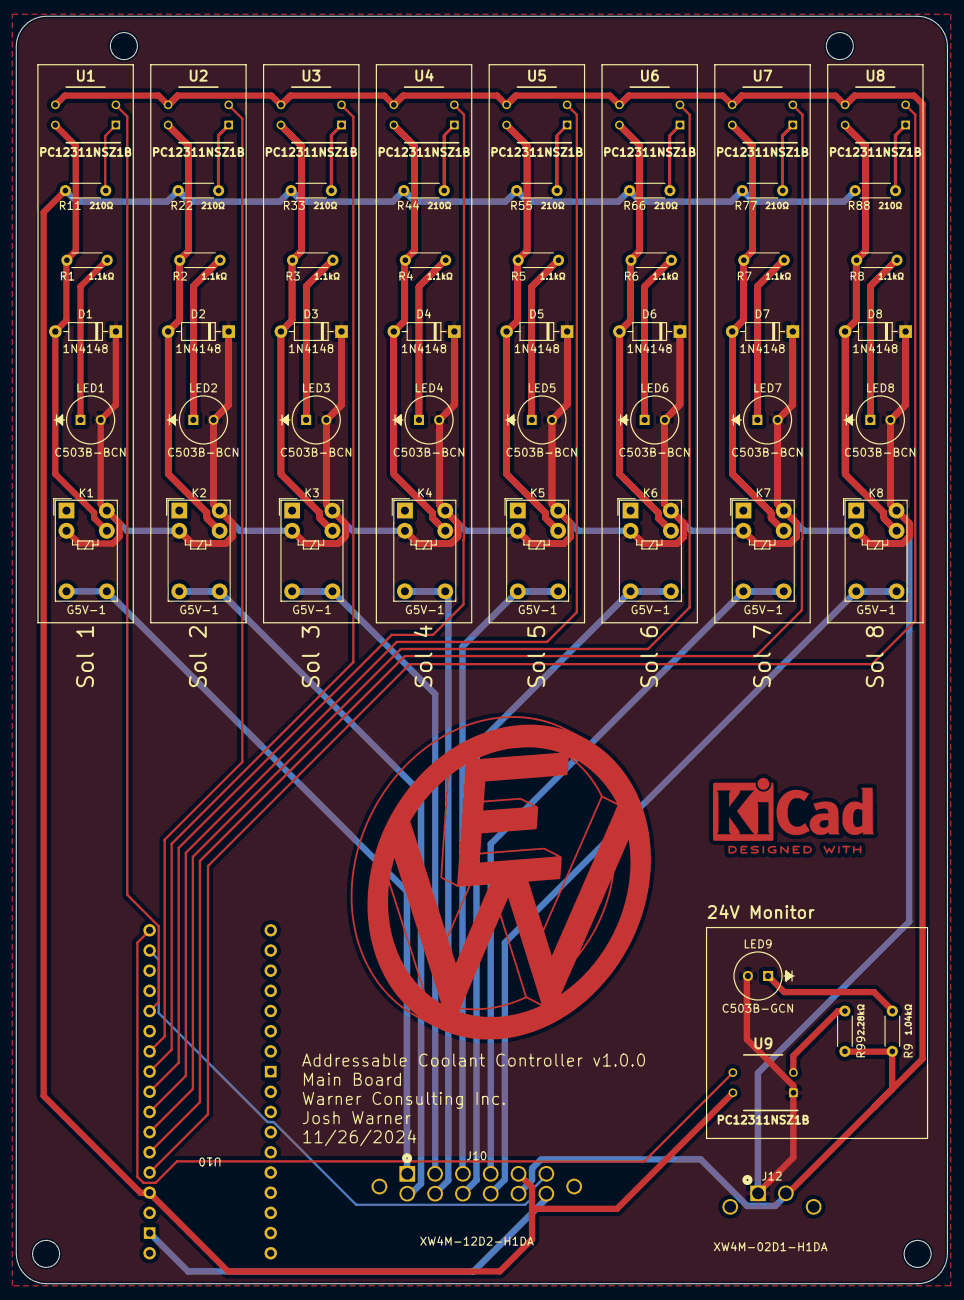
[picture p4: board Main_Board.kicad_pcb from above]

Board: 2 copper layers, 117.2 x 159.5 mm, 56 parts (0 on the bottom side), 48 nets.

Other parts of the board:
J10: XW4M-12D2-H1DA; xw4m-12d2-h1da
J12: XW4M-02D1-H1DA; xw4m-02d1-h1da
Main_Board: Board

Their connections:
+24V: J12.1; also elsewhere on the board
/Main_Board/IO13: J10.6; also elsewhere on the board
/Main_Board/MCU 3.3v: J10.5; also elsewhere on the board
/Main_Board/MCU GND: J10.12; also elsewhere on the board
/Main_Board/S1: J10.1; also elsewhere on the board
/Main_Board/S2: J10.7; also elsewhere on the board
/Main_Board/S3: J10.2; also elsewhere on the board
/Main_Board/S4: J10.8; also elsewhere on the board
/Main_Board/S5: J10.3; also elsewhere on the board
/Main_Board/S6: J10.9; also elsewhere on the board
/Main_Board/S7: J10.4; also elsewhere on the board
/Main_Board/S8: J10.10; also elsewhere on the board
GND: J10.11, J12.2; also elsewhere on the board

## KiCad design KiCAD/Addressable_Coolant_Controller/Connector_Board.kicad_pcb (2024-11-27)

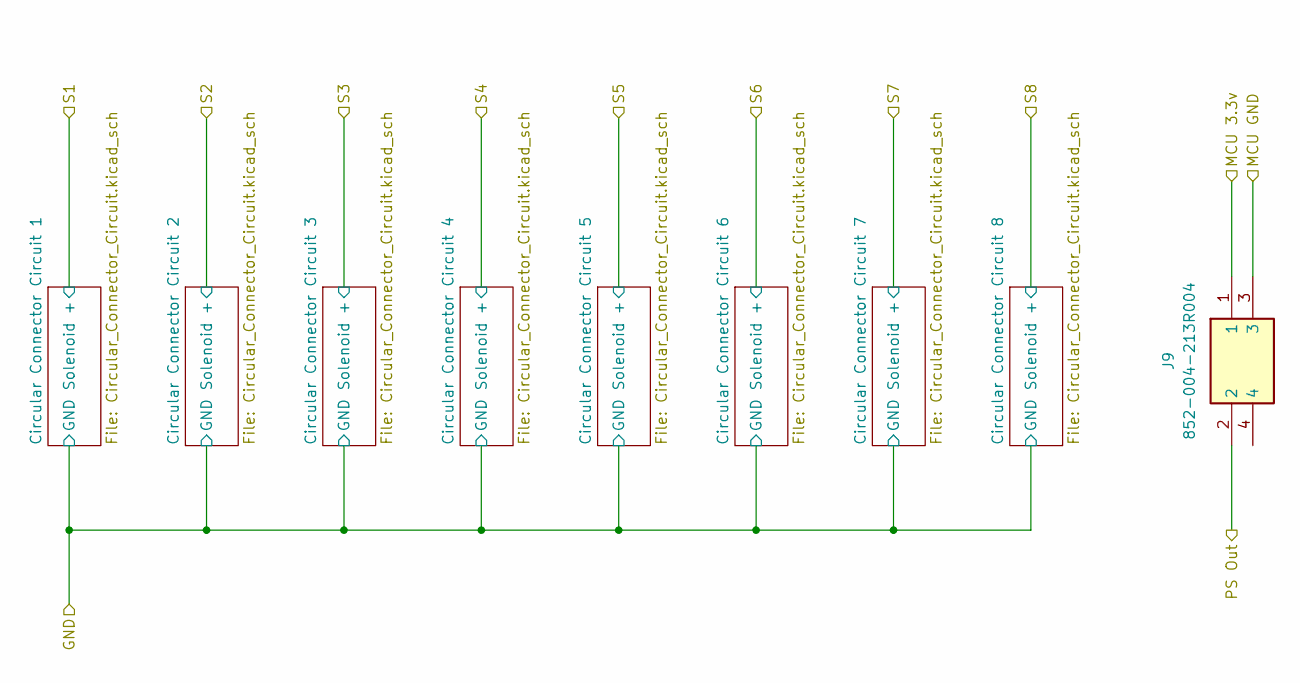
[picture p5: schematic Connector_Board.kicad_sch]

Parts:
J9: 852-004-213R004; 852004213R004; Manufacturer_Part_Number 852-004-213R004

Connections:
/Connector_Board/MCU 3.3v: J9.1; also elsewhere on the board
/Connector_Board/MCU GND: J9.3; also elsewhere on the board
/Connector_Board/PS Out: J9.2; also elsewhere on the board

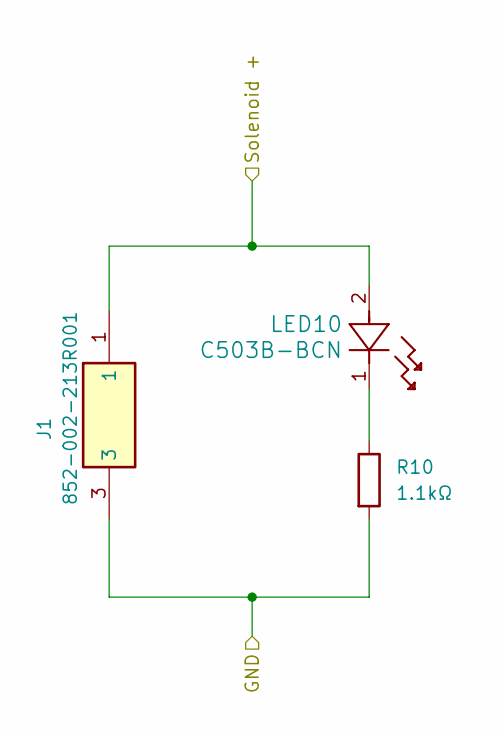
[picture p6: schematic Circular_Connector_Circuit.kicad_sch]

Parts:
J1: 852-002-213R001; Mouser Part Number 636-852-002-213R001
LED10: C503B-BCN; C503B_BCN_CV0Z0461
R10: 1.1kΩ; R_Axial_DIN0204_L3.6mm_D1.6mm_P5.08mm_Horizontal-JW

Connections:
/Connector_Board/GND: J1.3, R10.2; also elsewhere on the board
/Connector_Board/S1: J1.1, LED10.2; also elsewhere on the board
unnamed: LED10.1, R10.1

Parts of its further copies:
J2, J3, J4, J5, J6, J7, J8: 852-002-213R001; Mouser Part Number 636-852-002-213R001
LED20, LED30, LED40, LED50, LED60, LED70, LED80: C503B-BCN; C503B_BCN_CV0Z0461
R20, R30, R40, R50, R60, R70, R80: 1.1kΩ; R_Axial_DIN0204_L3.6mm_D1.6mm_P5.08mm_Horizontal-JW

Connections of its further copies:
/Connector_Board/GND: J2.3, J3.3, J4.3, J5.3, J6.3, J7.3, J8.3, R20.2, R30.2, R40.2, R50.2, R60.2, R70.2, R80.2; also elsewhere on the board
/Connector_Board/S2: J2.1, LED20.2; also elsewhere on the board
/Connector_Board/S3: J3.1, LED30.2; also elsewhere on the board
/Connector_Board/S4: J4.1, LED40.2; also elsewhere on the board
/Connector_Board/S5: J5.1, LED50.2; also elsewhere on the board
/Connector_Board/S6: J6.1, LED60.2; also elsewhere on the board
/Connector_Board/S7: J7.1, LED70.2; also elsewhere on the board
/Connector_Board/S8: J8.1, LED80.2; also elsewhere on the board
unnamed: LED20.1, R20.1
unnamed: LED30.1, R30.1
unnamed: LED40.1, R40.1
unnamed: LED50.1, R50.1
unnamed: LED60.1, R60.1
unnamed: LED70.1, R70.1
unnamed: LED80.1, R80.1

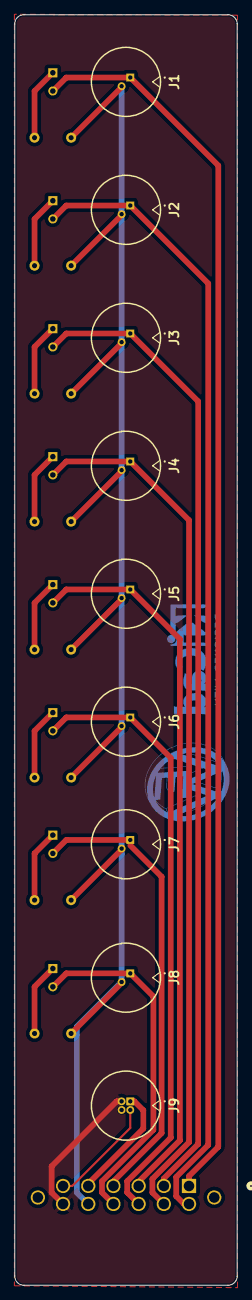
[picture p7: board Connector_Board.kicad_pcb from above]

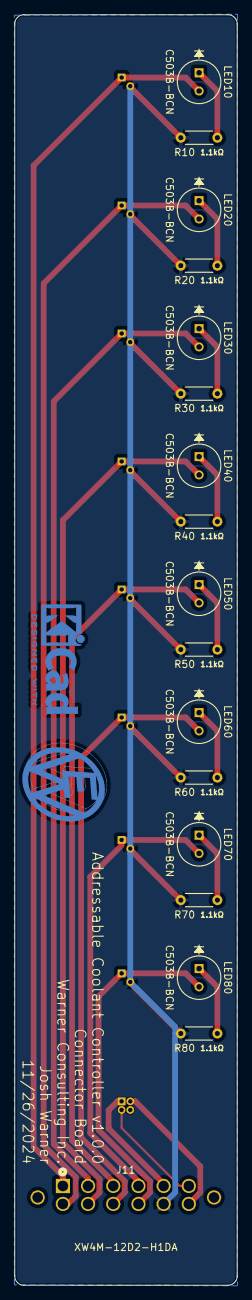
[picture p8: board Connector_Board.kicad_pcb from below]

Board: 2 copper layers, 30.9 x 176.5 mm, 27 parts (17 on the bottom side), 20 nets.

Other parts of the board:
Connector_Board: Board
J11: XW4M-12D2-H1DA; xw4m-12d2-h1da

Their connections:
/Connector_Board/GND: J11.11; also elsewhere on the board
/Connector_Board/MCU 3.3v: J11.5; also elsewhere on the board
/Connector_Board/MCU GND: J11.12; also elsewhere on the board
/Connector_Board/PS Out: J11.6; also elsewhere on the board
/Connector_Board/S1: J11.1; also elsewhere on the board
/Connector_Board/S2: J11.7; also elsewhere on the board
/Connector_Board/S3: J11.2; also elsewhere on the board
/Connector_Board/S4: J11.8; also elsewhere on the board
/Connector_Board/S5: J11.3; also elsewhere on the board
/Connector_Board/S6: J11.9; also elsewhere on the board
/Connector_Board/S7: J11.4; also elsewhere on the board
/Connector_Board/S8: J11.10; also elsewhere on the board

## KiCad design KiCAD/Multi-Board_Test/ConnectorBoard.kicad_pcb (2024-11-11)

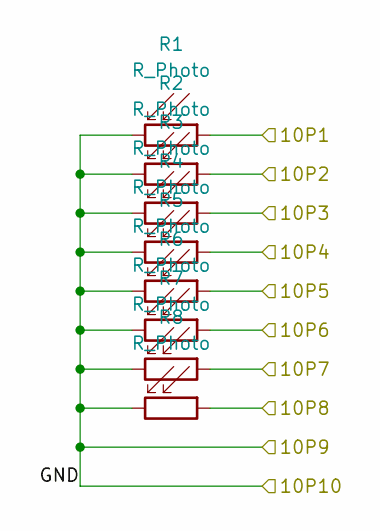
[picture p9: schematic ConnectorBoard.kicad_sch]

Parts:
R1, R2, R3, R4, R5, R6, R7, R8: R_Photo; R_Axial_DIN0204_L3.6mm_D1.6mm_P1.90mm_Vertical

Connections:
/Connector Board/10P1: R1.1; also elsewhere on the board
/Connector Board/10P2: R2.1; also elsewhere on the board
/Connector Board/10P3: R3.1; also elsewhere on the board
/Connector Board/10P4: R4.1; also elsewhere on the board
/Connector Board/10P5: R5.1; also elsewhere on the board
/Connector Board/10P6: R6.1; also elsewhere on the board
/Connector Board/10P7: R7.1; also elsewhere on the board
/Connector Board/10P8: R8.1; also elsewhere on the board
/Connector Board/GND: R1.2, R2.2, R3.2, R4.2, R5.2, R6.2, R7.2, R8.2; also elsewhere on the board

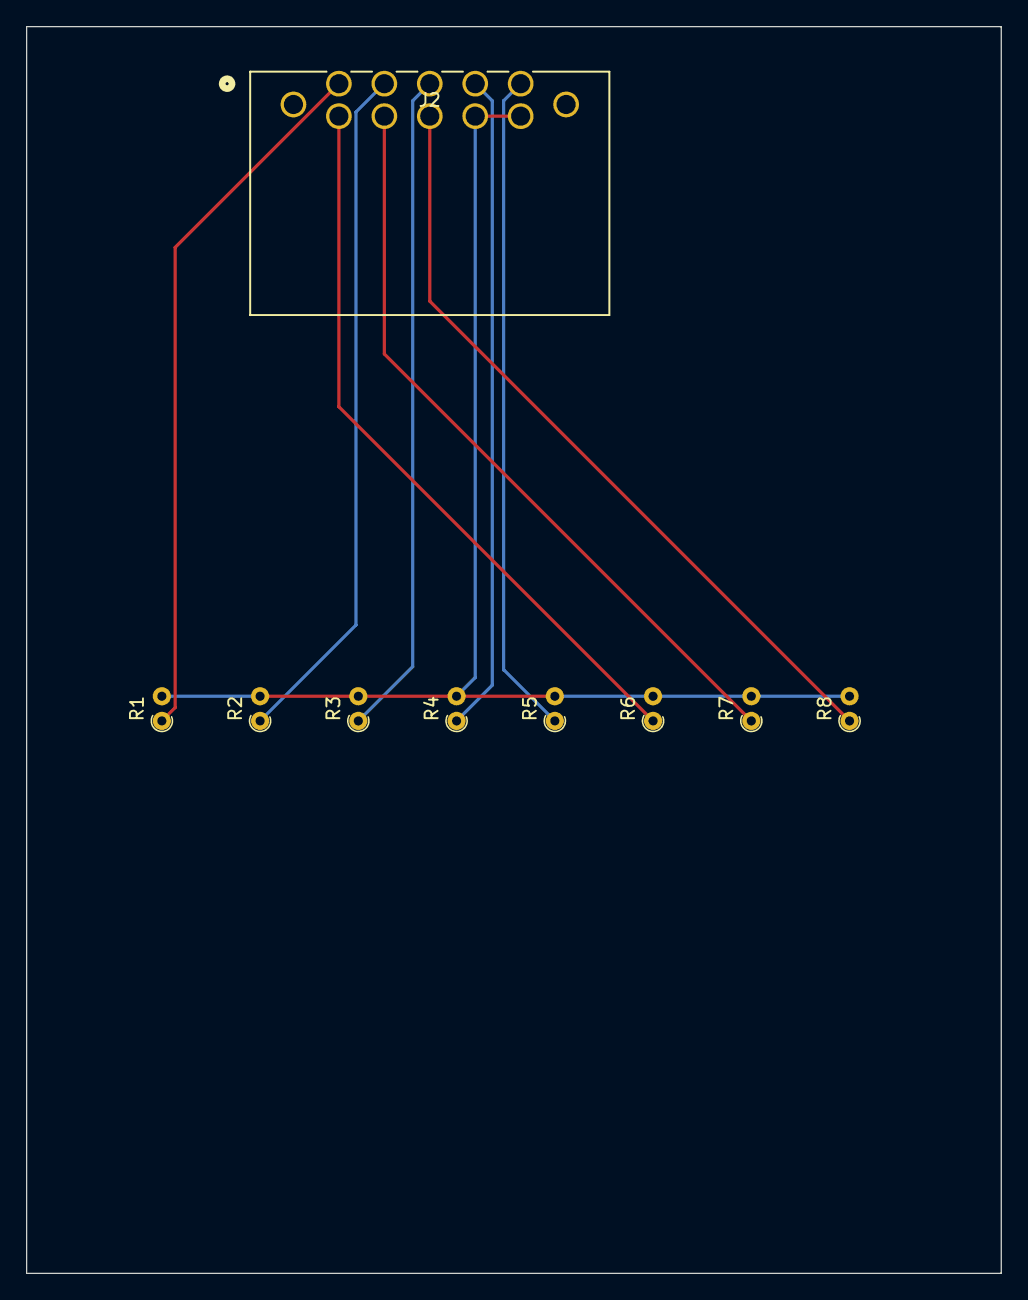
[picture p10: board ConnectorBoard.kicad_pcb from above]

Board: 2 copper layers, 75.1 x 96.0 mm, 10 parts (0 on the bottom side), 9 nets.

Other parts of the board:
B1: Board
J2: XW4M-10D2-H1DS; xw4m-10d2-h1ds

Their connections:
/Connector Board/10P1: J2.1; also elsewhere on the board
/Connector Board/10P2: J2.2; also elsewhere on the board
/Connector Board/10P3: J2.3; also elsewhere on the board
/Connector Board/10P4: J2.4; also elsewhere on the board
/Connector Board/10P5: J2.5; also elsewhere on the board
/Connector Board/10P6: J2.6; also elsewhere on the board
/Connector Board/10P7: J2.7; also elsewhere on the board
/Connector Board/10P8: J2.8; also elsewhere on the board
/Connector Board/GND: J2.9, J2.10; also elsewhere on the board

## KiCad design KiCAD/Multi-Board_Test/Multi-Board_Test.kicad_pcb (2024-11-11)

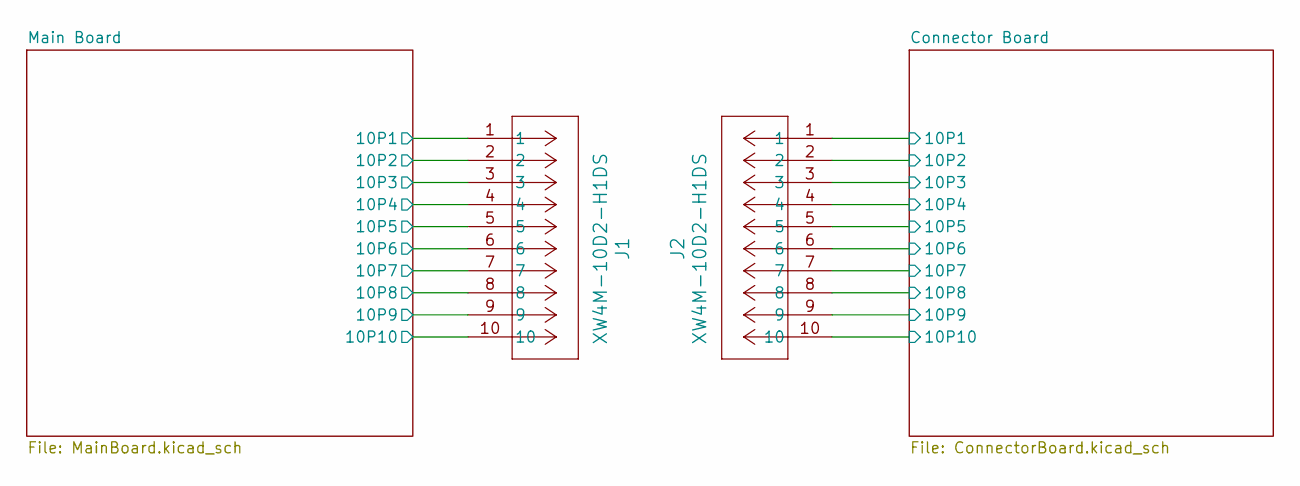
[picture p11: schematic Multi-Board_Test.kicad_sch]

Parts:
J1, J2: XW4M-10D2-H1DS; xw4m-10d2-h1ds

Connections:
/Connector Board/10P1: J2.1; also elsewhere on the board
/Connector Board/10P2: J2.2; also elsewhere on the board
/Connector Board/10P3: J2.3; also elsewhere on the board
/Connector Board/10P4: J2.4; also elsewhere on the board
/Connector Board/10P5: J2.5; also elsewhere on the board
/Connector Board/10P6: J2.6; also elsewhere on the board
/Connector Board/10P7: J2.7; also elsewhere on the board
/Connector Board/10P8: J2.8; also elsewhere on the board
/Connector Board/GND: J2.9, J2.10; also elsewhere on the board
/Main Board/10P1: J1.1; also elsewhere on the board
/Main Board/10P2: J1.2; also elsewhere on the board
/Main Board/10P3: J1.3; also elsewhere on the board
/Main Board/10P4: J1.4; also elsewhere on the board
/Main Board/10P5: J1.5; also elsewhere on the board
/Main Board/10P6: J1.6; also elsewhere on the board
/Main Board/10P7: J1.7; also elsewhere on the board
/Main Board/10P8: J1.8; also elsewhere on the board
/Main Board/GND: J1.9, J1.10; also elsewhere on the board

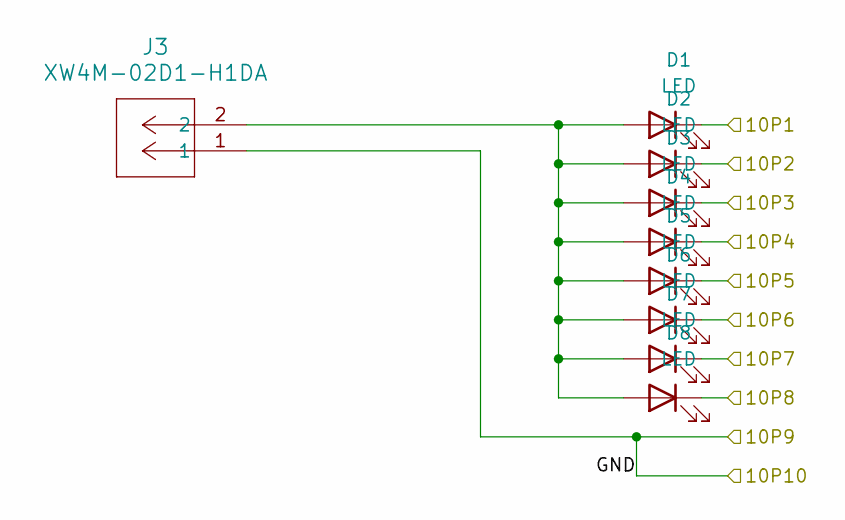
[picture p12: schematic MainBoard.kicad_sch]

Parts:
D1, D2, D3, D4, D5, D6, D7, D8: LED; LED_BL-FL7680RGB
J3: XW4M-02D1-H1DA; xw4m-02d1-h1da

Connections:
/Main Board/10P1: D1.1 (K); also elsewhere on the board
/Main Board/10P2: D2.1 (K); also elsewhere on the board
/Main Board/10P3: D3.1 (K); also elsewhere on the board
/Main Board/10P4: D4.1 (K); also elsewhere on the board
/Main Board/10P5: D5.1 (K); also elsewhere on the board
/Main Board/10P6: D6.1 (K); also elsewhere on the board
/Main Board/10P7: D7.1 (K); also elsewhere on the board
/Main Board/10P8: D8.1 (K); also elsewhere on the board
/Main Board/GND: J3.1; also elsewhere on the board
unnamed: D1.2 (A), D2.2 (A), D3.2 (A), D4.2 (A), D5.2 (A), D6.2 (A), D7.2 (A), D8.2 (A), J3.2


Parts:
R1, R2, R3, R4, R5, R6, R7, R8: R_Photo; R_Axial_DIN0204_L3.6mm_D1.6mm_P1.90mm_Vertical

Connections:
/Connector Board/10P1: R1.1; also elsewhere on the board
/Connector Board/10P2: R2.1; also elsewhere on the board
/Connector Board/10P3: R3.1; also elsewhere on the board
/Connector Board/10P4: R4.1; also elsewhere on the board
/Connector Board/10P5: R5.1; also elsewhere on the board
/Connector Board/10P6: R6.1; also elsewhere on the board
/Connector Board/10P7: R7.1; also elsewhere on the board
/Connector Board/10P8: R8.1; also elsewhere on the board
/Connector Board/GND: R1.2, R2.2, R3.2, R4.2, R5.2, R6.2, R7.2, R8.2; also elsewhere on the board


Board: 2 copper layers, 189.2 x 96.0 mm, 21 parts (0 on the bottom side), 19 nets.

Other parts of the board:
B1, B2: Board

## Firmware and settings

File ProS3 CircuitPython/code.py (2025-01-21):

import board
import neopixel
import time
import supervisor
import sys
import digitalio
import analogio
import microcontroller
import displayio
import terminalio
from adafruit_display_text import label
import adafruit_displayio_ssd1306

# Initialize NeoPixel LED
pix = neopixel.NeoPixel(board.NEOPIXEL, 1, auto_write=False)
pix.fill((0, 0, 0))

# Initialize OLED screen and draw a white border
displayio.release_displays()
oled_reset = board.D7

i2c = board.I2C()
display_bus = displayio.I2CDisplay(i2c, device_address=0x3D, reset=oled_reset)
WIDTH = 128
HEIGHT = 64
BORDER = 1

display = adafruit_displayio_ssd1306.SSD1306(display_bus, width=WIDTH, height=HEIGHT)
splash = displayio.Group()
display.root_group = splash

color_bitmap = displayio.Bitmap(WIDTH, HEIGHT, 1)
color_palette = displayio.Palette(1)
color_palette[0] = 0xFFFFFF  # White

bg_sprite = displayio.TileGrid(color_bitmap, pixel_shader=color_palette, x=0, y=0)
splash.append(bg_sprite)

inner_bitmap = displayio.Bitmap(WIDTH - BORDER * 2, HEIGHT - BORDER * 2, 1)
inner_palette = displayio.Palette(1)
inner_palette[0] = 0x000000  # Black
inner_sprite = displayio.TileGrid(inner_bitmap, pixel_shader=inner_palette, x=BORDER, y=BORDER)
splash.append(inner_sprite)

ToolNumberLabelArea = label.Label(terminalio.FONT, text=" " * 20, color=0xFFFFFF, scale=2)
ToolNumberLabelArea.anchor_point = (0.0, 0.0)
ToolNumberLabelArea.anchored_position = (2, 1)
splash.append(ToolNumberLabelArea)

PwrLabelArea = label.Label(terminalio.FONT, text=" " * 20, color=0xFFFFFF, scale=2)
PwrLabelArea.anchor_point = (0.0, 1)
PwrLabelArea.anchored_position = (2, 65)
splash.append(PwrLabelArea)

PresLabelArea = label.Label(terminalio.FONT, text=" " * 20, color=0xFFFFFF, scale=2)
PresLabelArea.anchor_point = (0.0, 0.5)
PresLabelArea.anchored_position = (2, 32)
splash.append(PresLabelArea)

pin_mappings = [
    (1, board.IO16),
    (2, board.IO0),
    (3, board.IO21),
    (4, board.IO5),
    (5, board.IO4),
    (6, board.IO3),
    (7, board.IO2),
    (8, board.IO1)
]

output_pins = {}
for number, pin_id in pin_mappings:
    pin = digitalio.DigitalInOut(pin_id)
    pin.direction = digitalio.Direction.OUTPUT
    pin.value = True  # Active low logic
    output_pins[number] = pin

pwr_pin = board.IO12
pwr_monitor = digitalio.DigitalInOut(pwr_pin)
pwr_monitor.direction = digitalio.Direction.INPUT
pwr_monitor.pull = digitalio.Pull.DOWN

pres_pin = board.IO13
pres_input = analogio.AnalogIn(pres_pin)

serial = sys.stdin
sys.stdout = sys.stdout  # Ensure stdout is set up for output

class StateMachine:
    def __init__(self):
        self.state = "IDLE"
        self.led_on_time = None
        self.oldData = None
        self.pwr_check_start = time.monotonic()
        self.pres_check_start = time.monotonic()
        self.status_report_time = time.monotonic()

    def update(self):
        current_time = time.monotonic()

        if self.state == "IDLE":
            self.check_power(current_time)
            self.check_pressure(current_time)
            self.read_serial(current_time)
            self.report_status(current_time)

        elif self.state == "PROCESS_SERIAL":
            self.process_serial_data()

        elif self.state == "BLINK_LED":
            self.blink_led(current_time)

    def check_power(self, current_time):
        if current_time - self.pwr_check_start >= 0.5:
            pwr_state = pwr_monitor.value
            pwr_text = "on" if pwr_state else "off"
            PwrLabelArea.text = 'Power: %s' % pwr_text
            self.pwr_check_start = current_time

    def check_pressure(self, current_time):
        if current_time - self.pres_check_start >= 0.5:
            pres_val = (((pres_input.value/65535)*3.3)-0.3968)/0.0258 # pressure (psi) = (((ADC_reading/65535)*V_ref)-V_offset)/Volt_per_PSI
            PresLabelArea.text = 'PSI: %d' % pres_val
            self.pres_check_start = current_time

    def read_serial(self, current_time):
        if supervisor.runtime.serial_bytes_available:
            data_in = serial.readline().strip()
            try:
                data_int = int(data_in)
                if data_int != self.oldData:
                    self.oldData = data_int
                    self.state = "PROCESS_SERIAL"
            except ValueError:
                print("Non-integer data")

    def report_status(self, current_time):
        if current_time - self.status_report_time >= 1.0:
            pwr_status = "on" if pwr_monitor.value else "off"
            pres_val = pres_input.value
            print('TOOL:%d PWR:%s PRES:%d' % (self.oldData if self.oldData else 0, pwr_status, pres_val))
            self.status_report_time = current_time

    def process_serial_data(self):
        if self.oldData is not None:
            ToolNumberLabelArea.text = 'Tool: %d' % self.oldData
            #print('%d' % self.oldData)  # Send tool number back over serial

            for pin in output_pins.values():
                pin.value = True

            if self.oldData in output_pins:
                output_pins[self.oldData].value = False

            pix.fill((0, 100, 0))
            pix.show()
            self.led_on_time = time.monotonic()
            self.state = "BLINK_LED"

    def blink_led(self, current_time):
        if self.led_on_time is not None and current_time - self.led_on_time >= 2.0:
            pix.fill((0, 0, 0))
            pix.show()
            self.led_on_time = None
            self.state = "IDLE"

state_machine = StateMachine()

print(microcontroller.cpu.reset_reason)

while True:
    state_machine.update()
    time.sleep(0.01)  # Prevent high CPU usage

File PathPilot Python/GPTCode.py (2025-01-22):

# coding=utf-8
from threading import Thread
import time
import glob
import serial
import linuxcnc
from ui_hooks import plugin, StateMachine, StateDescriptor

# Constants
SHORT_SLEEP_TIME = 1.0
LONG_SLEEP_TIME = 1.0
deviceName = "/dev/ProS3"
POWER_OFF_THRESHOLD = 5.0  # Seconds power can be off before pausing execution
TOOL_CHECK_DELAY = 2.0  # Seconds after tool change to check tool number
PRESSURE_THRESHOLD = 20.0  # PSI minimum pressure threshold
PRESSURE_DROP_DURATION = 10.0  # Seconds pressure must be below threshold before stopping execution
CONNECTION_LOSS_THRESHOLD = 10.0  # Seconds connection loss before stopping execution

# Define states
NOT_CONNECTED = 0
CONNECTED_IDLE = 1
TOOL_CHANGED = 2
PROCESSING_RESPONSE = 3

UPDATE_PERIOD = 1.0

class UserPlugin(plugin):
    def __init__(self):
        plugin.__init__(self, 'ProS3Cool with State Machine')

        # Initialize serial object
        self.comPort = serial.Serial()
        self.ShowMsg('comPort created')
        self.last_status_time = time.time()
        self.last_power_on_time = time.time()
        self.last_tool_check_time = None
        self.last_pressure_drop_time = None
        self.last_connection_loss_time = None
        self.stat = linuxcnc.stat()
        self.command = linuxcnc.command()
        
        # Track the last tool and microcontroller-reported values
        self.lastTool = 0
        self.microcontrollerTool = None
        self.power_status = "on"  # Default power status
        self.pressure_value = 100.0  # Default pressure value (high enough to not trigger)

        # Start the state machine thread
        self.TinyS3Thread = Thread(target=self.UpdateStateMachine)
        self.TinyS3Thread.daemon = True
        self.TinyS3Thread.start()

    def TryToConnect(self):
        devices = glob.glob(deviceName)
        self.ShowMsg('Found devices: %s' % devices)
        if not devices:
            return False

        for symlink in devices:
            try:
                self.comPort.port = symlink
                self.comPort.baudrate = 115200
                self.comPort.timeout = 1
                self.comPort.open()
                self.ShowMsg('Connected to %s' % symlink)
                return True
            except serial.SerialException as e:
                self.ShowMsg('Failed to open %s: %s' % (symlink, str(e)))
        return False

    def UpdateStateMachine(self):
        machine = StateMachine()
        machine.AddState(NOT_CONNECTED, StateDescriptor("Not Connected", self.EnterNotConnected, self.UpdateNotConnected, None))
        machine.AddState(CONNECTED_IDLE, StateDescriptor("Connected Idle", self.EnterConnectedIdle, self.UpdateConnectedIdle, None))
        machine.AddState(TOOL_CHANGED, StateDescriptor("Tool Changed", self.EnterToolChanged, self.UpdateToolChanged, None))
        machine.AddState(PROCESSING_RESPONSE, StateDescriptor("Processing Response", self.EnterProcessingResponse, self.UpdateProcessingResponse, None))
        machine.ChangeState(NOT_CONNECTED)

        while True:
            time.sleep(UPDATE_PERIOD)
            self.halStatus.poll()
            self.read_status_from_microcontroller()
            self.check_errors()
            machine.Update()

    def read_status_from_microcontroller(self):
        if self.comPort.is_open and self.comPort.in_waiting:
            line = self.comPort.readline().decode('utf-8').strip()
            self.process_status_message(line)

    def process_status_message(self, message):
        self.last_status_time = time.time()
        try:
            parts = message.split()
            status_data = {}
            for part in parts:
                key, value = part.split(":")
                status_data[key] = value

            self.microcontrollerTool = int(status_data.get("TOOL", 0))
            self.power_status = status_data.get("PWR", "off")
            self.pressure_value = float(status_data.get("PRES", 100.0))

            self.ShowMsg("Received: Tool: %d, Power: %s, Pressure: %.2f" % (self.microcontrollerTool, self.power_status, self.pressure_value))
        except Exception as e:
            self.ShowMsg("Error parsing status message: %s" % str(e))

    def check_errors(self):
        self.stat.poll()
        current_time = time.time()
        
        # Check power status first
        if self.stat.task_mode == linuxcnc.MODE_AUTO:
            if self.power_status == "off" and (current_time - self.last_power_on_time > POWER_OFF_THRESHOLD):
                self.ShowMsg("Power has been off for too long! Pausing execution.")
                self.command.abort()
            elif self.power_status == "on":
                self.last_power_on_time = current_time
        
        # Check tool mismatch 2 seconds after tool change
        if self.last_tool_check_time and (current_time - self.last_tool_check_time >= TOOL_CHECK_DELAY):
            if self.microcontrollerTool is not None and self.microcontrollerTool != self.stat.tool_in_spindle:
                self.ShowMsg("Tool mismatch detected! Pausing execution.")
                self.command.abort()
            self.last_tool_check_time = None  # Reset after check
        
        # Check pressure drop if coolant is on
        if self.stat.flood and self.pressure_value < PRESSURE_THRESHOLD:
            if self.last_pressure_drop_time is None:
                self.last_pressure_drop_time = current_time  # Start tracking time of pressure drop
            elif (current_time - self.last_pressure_drop_time) >= PRESSURE_DROP_DURATION:
                self.ShowMsg("Coolant pressure too low for too long! Pausing execution.")
                self.command.abort()
        else:
            self.last_pressure_drop_time = None  # Reset timer when pressure recovers or coolant is off
        
        # Check for connection loss
        if self.stat.task_mode == linuxcnc.MODE_AUTO and not self.comPort.is_open:
            if self.last_connection_loss_time is None:
                self.last_connection_loss_time = current_time  # Start tracking connection loss time
            elif (current_time - self.last_connection_loss_time) >= CONNECTION_LOSS_THRESHOLD:
                self.ShowMsg("Connection lost for too long! Pausing execution.")
                self.command.abort()
        else:
            self.last_connection_loss_time = None  # Reset timer if connection is restored

    def EnterNotConnected(self, machine):
        self.ShowMsg("Entering state 'Not Connected'")
        self.comPort.close()

    def UpdateNotConnected(self, machine):
        if self.TryToConnect():
            machine.ChangeState(CONNECTED_IDLE)

    def EnterConnectedIdle(self, machine):
        self.ShowMsg("Entering state 'Connected Idle'")

    def UpdateConnectedIdle(self, machine):
        if not self.comPort.is_open:
            machine.ChangeState(NOT_CONNECTED)
            return
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

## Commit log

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2024-01-25 Implemented 2 way serial communication
    Implemented serial communication on the device side. Needed to add some error handling code and especially needed to disable the modemmanager service in linux
    [ProS3Cool_plugin.py, code.py]
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2024-02-05 Update code.py
    Added watchdog code and reset reason code.
    [code.py]
2024-02-08 Update code.py
    Got relay control working. Need to fix LED blink code. Removed watchdog for testing purposes.
    [code.py]
2024-02-12 Added KiCAD files to repository
    [ColletAutoFeed_RelayBoard.kicad_pcb, ColletAutoFeed_RelayBoard.kicad_sch, Relay_Circuit.kicad_sch]
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2024-02-12 Added 24v Monitor Circuit
    Added hierarchical sheet with 24v monitor circuit. Added 4 pin power connector for 24v input. Same family connector as ribbon cable connector for relay to solenoid connections out to daughter board.
    [24v_Monitor_Circuit.kicad_sch, ColletAutoFeed_RelayBoard.kicad_sch]
2024-02-13 Ran Annotation and ERC
    Annotated and ran Electronics Rules Checker. Started assigning footprints and appropriate step files to said footprints. Added custom KiCAD library folder to Github.
    [24v_Monitor_Circuit.kicad_sch, 690367190472.step, 690367191672.step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]
2024-02-14 Removed Custom Libraries
    Setting up for using git submodule
    [690367190472.step, 690367191672.step]
2024-02-14 Added ProS3 symbol, footprint, and step file from submodule
    [ColletAutoFeed_RelayBoard.kicad_sch]
2024-02-15 Switched to TE AMP-Latch connector
    Removed Wurth ribbon cable connector and replaced with TE AMP-Latch connector after physically evaluating both.
    [ColletAutoFeed_RelayBoard.kicad_sch]
2024-02-15 Assigned footprint to pin header
    [ColletAutoFeed_RelayBoard.kicad_sch]
2024-02-15 Added borders and labels to schematic
    [ColletAutoFeed_RelayBoard.kicad_sch]
2024-02-17 Started PCB layout
    [24v_Monitor_Circuit.kicad_sch, ColletAutoFeed_RelayBoard.kicad_pcb, ColletAutoFeed_RelayBoard.kicad_sch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]
2024-02-17 Changed to tht LEDs and added LED to power monitor circuit
    [24v_Monitor_Circuit.kicad_sch, ColletAutoFeed_RelayBoard.kicad_pcb, Relay_Circuit.kicad_sch]
2024-02-20 Started routing
    [24v_Monitor_Circuit.kicad_sch, ColletAutoFeed_RelayBoard.kicad_pcb, Relay_Circuit.kicad_sch]
2024-02-20 Continued routing
    [ColletAutoFeed_RelayBoard.kicad_pcb]
2024-02-20 Added ground and power planes
    [ColletAutoFeed_RelayBoard.kicad_pcb]
2024-02-21 Continued working on routing
    [ColletAutoFeed_RelayBoard.kicad_pcb, Relay_Circuit.kicad_sch]
2024-02-25 Updated resistor footprints to include values
    [24v_Monitor_Circuit.kicad_sch, ColletAutoFeed_RelayBoard.kicad_pcb, Relay_Circuit.kicad_sch]
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2024-03-06 Combined 2 pin power input into ribbon cable
    [ColletAutoFeed_RelayBoard.kicad_sch]
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2024-10-15 Replaced ribbon cable connector with 10-pin molex
    [ColletAutoFeed_RelayBoard.kicad_pcb, ColletAutoFeed_RelayBoard.kicad_sch]
2024-10-17 Updated board to new size
    Updated board outline, stripped all old routing, added 2 pin omron power connector
    [ColletAutoFeed_RelayBoard.kicad_pcb, ColletAutoFeed_RelayBoard.kicad_sch]
2024-10-22 Placed components and routed traces on PCB
    Placed components and completed initial routing. Still need to add power and ground planes and figure out silkscreen.
    [ColletAutoFeed_RelayBoard.kicad_pcb, ColletAutoFeed_RelayBoard.kicad_sch]
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2024-10-23 Replaced opto-isolator with through hole version
    [ColletAutoFeed_RelayBoard.kicad_pcb, Relay_Circuit.kicad_sch]
2024-10-24 Added rectangle representing screen
    [ColletAutoFeed_RelayBoard.kicad_pcb]
2024-10-25 Replaced remaining opto-isolator and started silkscreen
    [24v_Monitor_Circuit.kicad_sch, ColletAutoFeed_RelayBoard.kicad_pcb, ColletAutoFeed_RelayBoard.kicad_sch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]
2024-10-25 Fixed Silkscreen Labels for Components
    [24v_Monitor_Circuit.kicad_sch, ColletAutoFeed_RelayBoard.kicad_pcb, ColletAutoFeed_RelayBoard.kicad_sch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]
2024-10-28 Shortened LED legs and updated the submodule to reflect
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2024-10-28 Added Logo to silkscreen
    [ColletAutoFeed_RelayBoard.kicad_pcb]
2024-10-29 Added zones and labels to Silkscreen
    [ColletAutoFeed_RelayBoard.kicad_pcb]
2024-10-30 Renamed to Addressable Coolant Controller v1.0.0
    [Addressable Coolant Controller v1.0.0.kicad_pcb, Addressable Coolant Controller v1.0.0.kicad_sch]
2024-10-30 Changed project name to Addressable Coolant Controller
    [1761685-6.step, 206832-0202.stp, 24v_Monitor_Circuit.kicad_sch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]
2024-10-31 Created Multi-Board Test Project
    [ConnectorBoard.kicad_sch, MainBoard.kicad_sch, Multi-Board Test.kicad_pcb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]
2024-11-11 Worked on multi board workflow
    [ConnectorBoard.kicad_pcb, ConnectorBoard.kicad_sch, MainBoard.kicad_sch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]
2024-11-11 Changing project name to "Addressable_Coolant_Controller"
    Removed spaces from project name to avoid issues with file system wonkiness.
    [1761685-6.step, 206832-0202.stp, 24v_Monitor_Circuit.kicad_sch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]
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2024-11-11 Removing broken submodule
    [1761685-6.step, 206832-0202.stp, C503B_BCN_CV0Z0461.STEP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]
2024-11-12 Updating KiCAD project to multi-board structure
    [24v_Monitor_Circuit.kicad_sch, Addressable_Coolant_Controller.kicad_sch, Main_Board.kicad_sch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]
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2024-11-14 Updating wiring positions to match 12 pin connector
    [Addressable_Coolant_Controller.kicad_sch]
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2024-11-14 Added voltage divider and changed to 12 pin connectors
    [24v_Monitor_Circuit.kicad_sch, Addressable_Coolant_Controller.kicad_sch, Main_Board.kicad_sch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]
2024-11-14 Fixed broken netclasses, removed voltage divider circuit
    [24v_Monitor_Circuit.kicad_sch, Addressable_Coolant_Controller.kicad_sch, Connector_Board.kicad_sch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]
2024-11-19 Added hierarchical labels to connector board
    [Addressable_Coolant_Controller.kicad_sch, Connector_Board.kicad_sch]
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2024-11-22 Added second board outline and circular connectors
    [24v_Monitor_Circuit.kicad_sch, Addressable_Coolant_Controller-Routed-Backup-Reference.kicad_pcb, Addressable_Coolant_Controller.kicad_pcb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]
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2024-11-25 Routed connector PCB and fixed components designators
    [24v_Monitor_Circuit.kicad_sch, Addressable_Coolant_Controller.kicad_pcb, Addressable_Coolant_Controller.kicad_sch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]
2024-11-26 Added LEDs to connector board, and moved to hierarchical sheet
    [Addressable_Coolant_Controller.kicad_pcb, Addressable_Coolant_Controller.kicad_sch, Circular_Connector_Circuit.kicad_sch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]
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2024-11-26 Updating Cree LED footprints with STEP files
    [24v_Monitor_Circuit.kicad_sch, Addressable_Coolant_Controller.kicad_pcb, Circular_Connector_Circuit.kicad_sch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]
2024-11-26 Updating PC123 footprint with STEP file
    [Addressable_Coolant_Controller.kicad_pcb]
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2024-11-26 Removing overhanging silkscreen from Omron footprints
    [Addressable_Coolant_Controller.kicad_pcb]
2024-11-26 updating 2-pin Omron with square pin 1
    [Addressable_Coolant_Controller.kicad_pcb]
2024-11-27 Finalized board design and exported for ordering
    [Addressable_Coolant_Controller.kicad_pcb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]
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2025-01-20 Added power and tool error checks
    [ProS3Cool_plugin.py, code.py]
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2025-01-22 Added plugin side connection error gcode pause
    [GPTCode.py, ProS3Cool_plugin.py]
